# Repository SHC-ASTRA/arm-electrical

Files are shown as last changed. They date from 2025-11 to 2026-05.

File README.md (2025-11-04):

# Arm Electrical



Includes the KiCAD files for the Socket and Digit PCBs; Socket is located at the base of Arm and controls the Arm's main joints, Digit is located at the end of Arm and controls Wrist and End Effector.

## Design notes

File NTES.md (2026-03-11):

REVs two on bottom two on wall. PCB mounted in spost as current; have esp face outawrds; 
Digit,Digit BATT, and digit CAN near current leds
Encoders in same spot?
fan ports on side of leds.

28.2 mm width
56.5 mm hieght
26.0 mm pins outside width 
54.0 mm pins outside hieght
03.2 mm distance between pins outer
01.9 mm distance between pins inner
00.6 mm pin width

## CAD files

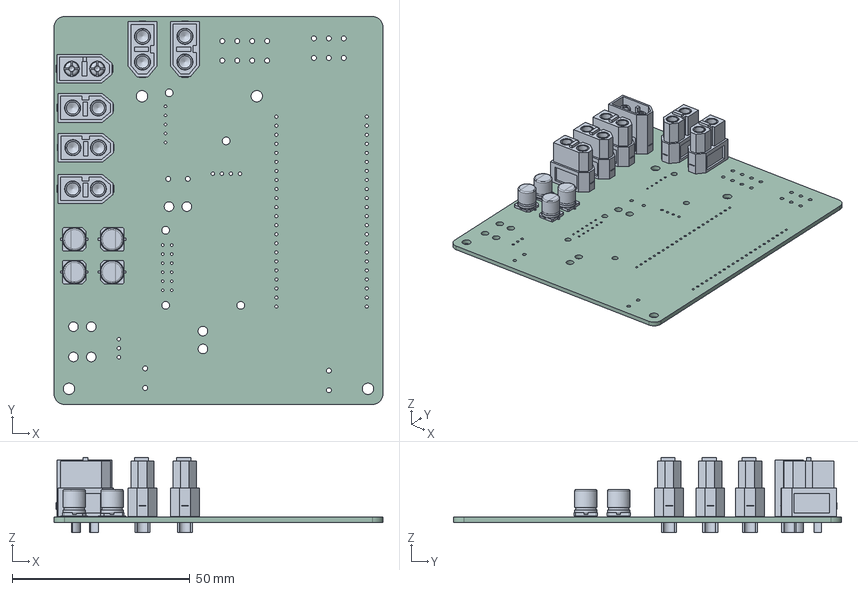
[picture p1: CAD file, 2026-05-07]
Arm/ArmV2.step
92.4 x 109.0 x 21.2 mm
AMASS_XT60-F_1x02_P7.2mm_Vertical x 5
CP_Elec_6.3x7.7 x 4
AMASS_XT60-M_1x02_P7.2mm_Vertical
Arm_PCB

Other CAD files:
Arm/Arm.step

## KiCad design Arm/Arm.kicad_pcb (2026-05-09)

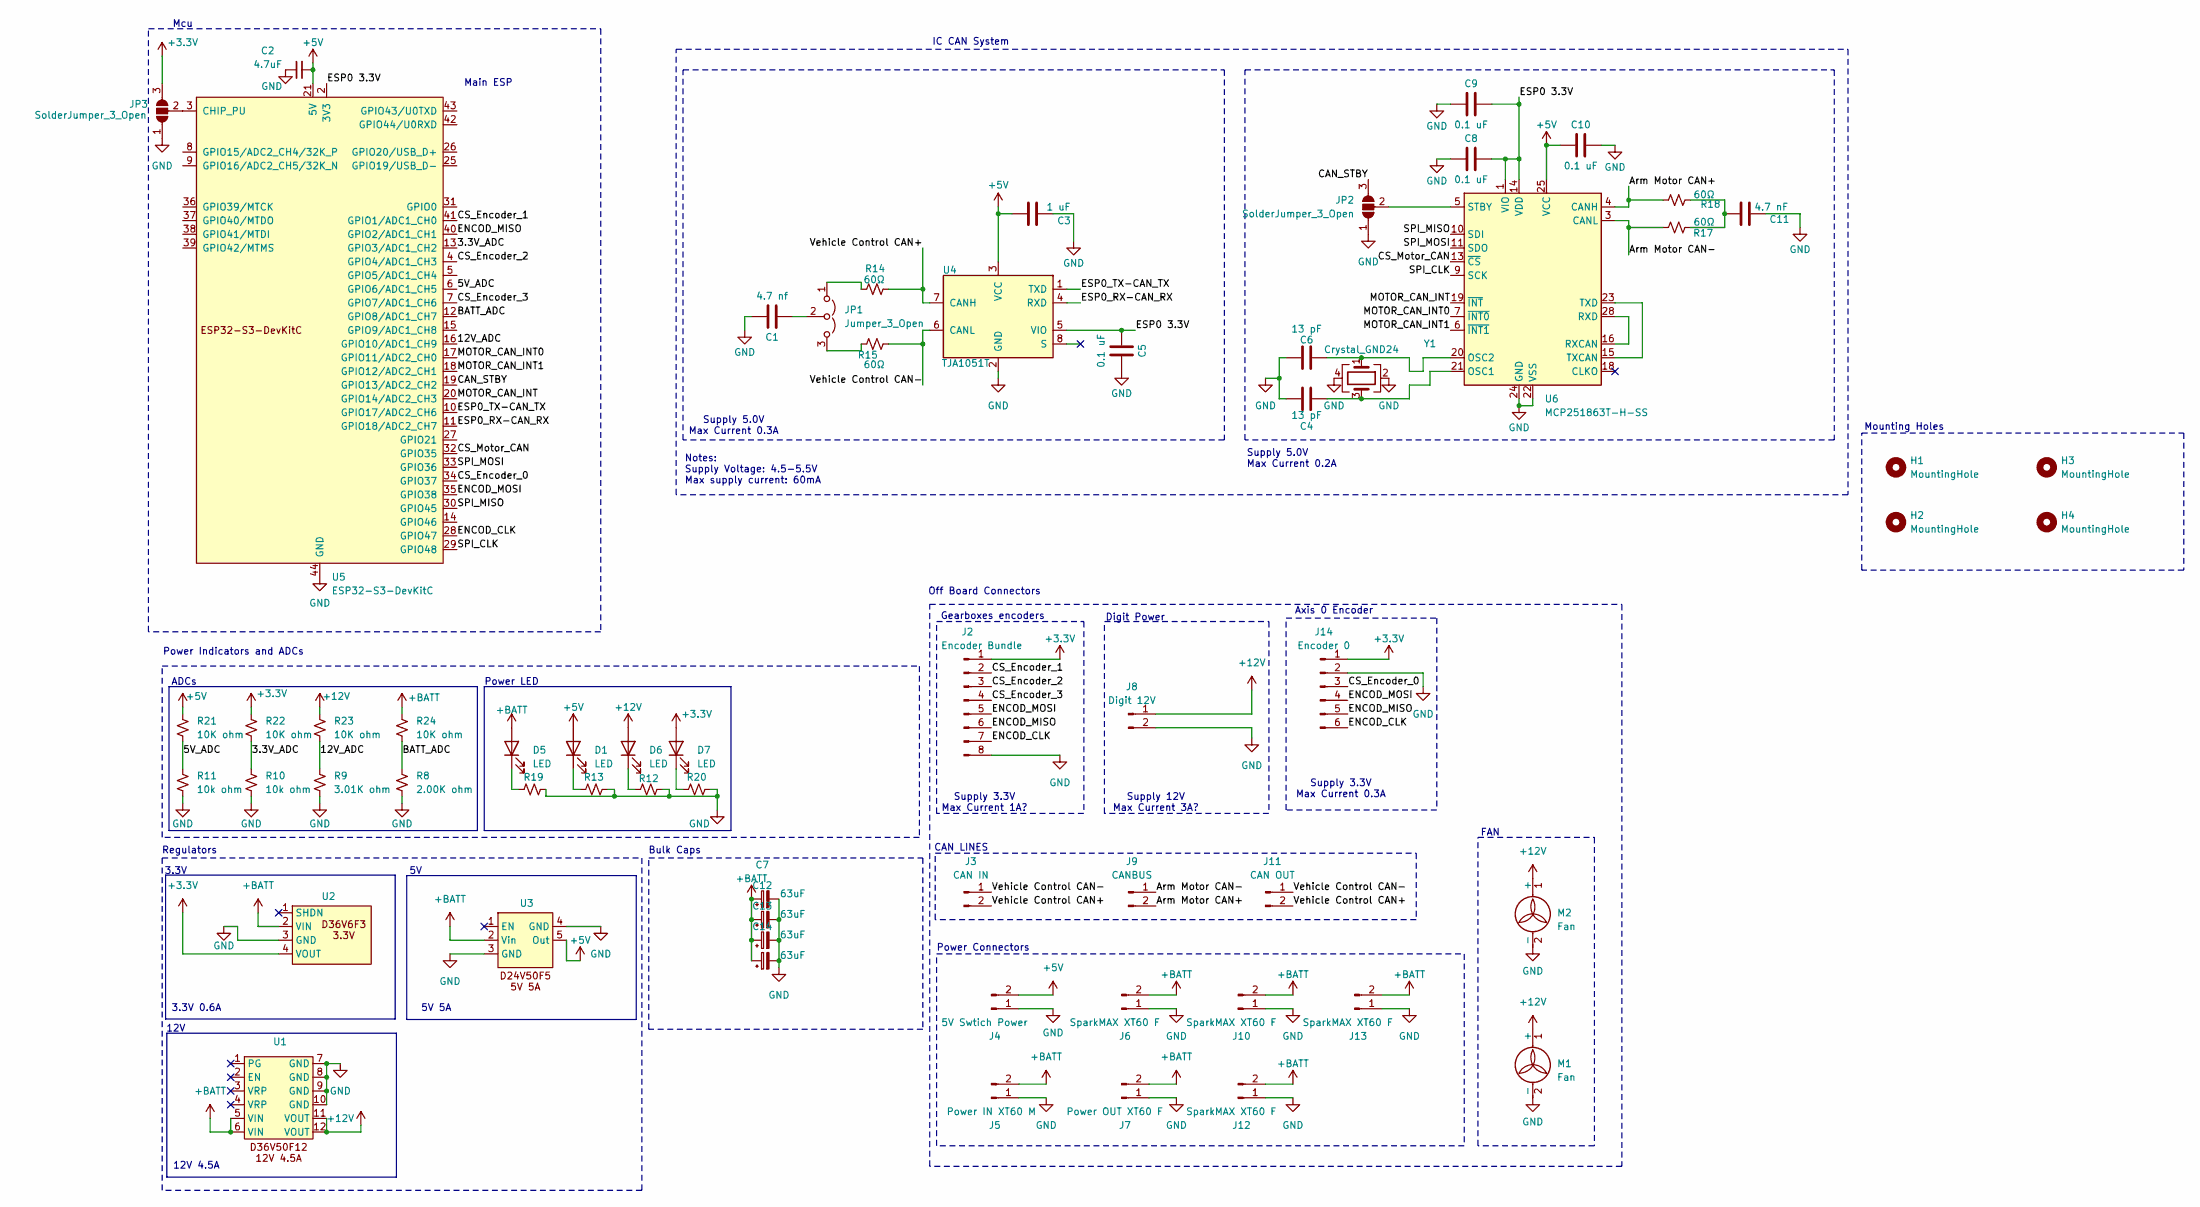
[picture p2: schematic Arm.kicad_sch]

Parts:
C1: 4.7 nf; C_0603_1608Metric_Pad1.08x0.95mm_HandSolder
C2: 4.7uF; C_0603_1608Metric_Pad1.08x0.95mm_HandSolder
C3: 1 uF; C_0603_1608Metric_Pad1.08x0.95mm_HandSolder
C4, C6: 13 pF; C_0603_1608Metric_Pad1.08x0.95mm_HandSolder
C5, C8, C9, C10: 0.1 uF; C_0603_1608Metric_Pad1.08x0.95mm_HandSolder
C7, C12, C13, C14: 63uF; CP_Elec_6.3x7.7
C11: 4.7 nF; C_0603_1608Metric_Pad1.08x0.95mm_HandSolder
D1, D5, D6, D7: LED; LED_0603_1608Metric_Pad1.05x0.95mm_HandSolder
H1, H2, H3, H4: MountingHole; MountingHole_3.2mm_M3_DIN965_Pad_TopBottom
J2: Encoder Bundle; Molex_Mini-Fit_Jr_5566-08A_2x04_P4.20mm_Vertical
J3: CAN IN; AMASS_XT30U-F_1x02_P5.0mm_Vertical
J4: 5V Swtich Power; Molex_Mini-Fit_Jr_5566-02A_2x01_P4.20mm_Vertical
J5: Power IN XT60 M; AMASS_XT60-M_1x02_P7.20mm_Vertical
J6, J10, J12, J13: SparkMAX XT60 F; AMASS_XT60-F_1x02_P7.20mm_Vertical
J7: Power OUT XT60 F; AMASS_XT60-F_1x02_P7.20mm_Vertical
J8: Digit 12V; AMASS_XT30U-F_1x02_P5.0mm_Vertical
J9: CANBUS; AMASS_XT30U-F_1x02_P5.0mm_Vertical
J11: CAN OUT; AMASS_XT30U-F_1x02_P5.0mm_Vertical
J14: Encoder 0; Molex_Mini-Fit_Jr_5566-06A_2x03_P4.20mm_Vertical
JP1: Jumper_3_Open; PinHeader_1x03_P2.54mm_Vertical
JP2, JP3: SolderJumper_3_Open; SolderJumper-3_P1.3mm_Open_RoundedPad1.0x1.5mm
M1, M2: Fan; Molex_Mini-Fit_Jr_5566-02A_2x01_P4.20mm_Vertical
R8: 2.00K ohm; R_0603_1608Metric_Pad0.98x0.95mm_HandSolder
R9: 3.01K ohm; R_0603_1608Metric_Pad0.98x0.95mm_HandSolder
R10, R11: 10k ohm; R_0603_1608Metric_Pad0.98x0.95mm_HandSolder
R12, R13, R20: R_Small_US; R_0603_1608Metric_Pad0.98x0.95mm_HandSolder
R14, R15, R17, R18: 60Ω; R_0603_1608Metric_Pad0.98x0.95mm_HandSolder
R19: 2k ohm; R_0603_1608Metric_Pad0.98x0.95mm_HandSolder
R21, R22, R23, R24: 10K ohm; R_0603_1608Metric_Pad0.98x0.95mm_HandSolder
U1: D36V50F12
U2: D36V6F3 3.3V
U3: D24V50F5
U4: TJA1051T; SOIC-8_3.9x4.9mm_P1.27mm
U5: ESP32-S3-DevKitC
U6: MCP251863T-H-SS; SSOP-28_5.3x10.2mm_P0.65mm
Y1: Crystal_GND24; Crystal_SMD_3225-4Pin_3.2x2.5mm_HandSoldering

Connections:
+3.3V: D7.2 (A), J2.1, J14.1, JP3.3 (B), R22.1, U2.4 (VOUT)
+5V: C2.2, C3.1, C10.2, D1.2 (A), J4.2, R21.1, U3.5 (Out), U4.3 (VCC), U5.21 (5V), U6.25 (VCC)
+12V: D6.2 (A), J8.1, M1.1 (+), M2.1 (+), R23.1, U1.11 (VOUT), U1.12 (VOUT)
+BATT: C7.1, C12.1, C13.1, C14.1, D5.2 (A), J5.2, J6.2, J7.2, J10.2, J12.2, J13.2, R24.1, U1.5 (VIN), U1.6 (VIN), U2.2 (VIN), U3.2 (Vin)
/3.3V_ADC: R10.1, R22.2, U5.13 (GPIO3/ADC1_CH2)
/5V_ADC: R11.1, R21.2, U5.6 (GPIO6/ADC1_CH5)
/12V_ADC: R9.1, R23.2, U5.16 (GPIO10/ADC1_CH9)
/Arm Motor CAN+: J9.2, R18.2, U6.4 (CANH)
/Arm Motor CAN-: J9.1, R17.1, U6.3 (CANL)
/BATT_ADC: R8.1, R24.2, U5.12 (GPIO8/ADC1_CH7)
/CAN_STBY: JP2.3 (B), U5.19 (GPIO13/ADC2_CH2)
/CS_Encoder_0: J14.3, U5.34 (GPIO37)
/CS_Encoder_1: J2.2, U5.41 (GPIO1/ADC1_CH0)
/CS_Encoder_2: J2.3, U5.4 (GPIO4/ADC1_CH3)
/CS_Encoder_3: J2.4, U5.7 (GPIO7/ADC1_CH6)
/CS_Motor_CAN: U5.32 (GPIO35), U6.13 (~CS)
/ENCOD_CLK: J2.7, J14.6, U5.28 (GPIO47)
/ENCOD_MISO: J2.6, J14.5, U5.40 (GPIO2/ADC1_CH1)
/ENCOD_MOSI: J2.5, J14.4, U5.35 (GPIO38)
/ESP0 3.3V: C5.2, C8.1, C9.1, U4.5 (VIO), U5.1 (3V3), U5.2 (3V3), U6.1 (VIO), U6.14 (VDD)
/ESP0_RX-CAN_RX: U4.4 (RXD), U5.11 (GPIO18/ADC2_CH7)
/ESP0_TX-CAN_TX: U4.1 (TXD), U5.10 (GPIO17/ADC2_CH6)
/MOTOR_CAN_INT: U5.20 (GPIO14/ADC2_CH3), U6.19 (~INT)
/MOTOR_CAN_INT0: U5.17 (GPIO11/ADC2_CH0), U6.7 (~INT0)
/MOTOR_CAN_INT1: U5.18 (GPIO12/ADC2_CH1), U6.6 (~INT1)
/SPI_CLK: U5.29 (GPIO48), U6.9 (SCK)
/SPI_MISO: U5.30 (GPIO45), U6.10 (SDI)
/SPI_MOSI: U5.33 (GPIO36), U6.11 (SDO)
/Vehicle Control CAN+: J3.2, J11.2, R14.1, U4.7 (CANH)
/Vehicle Control CAN-: J3.1, J11.1, R15.2, U4.6 (CANL)
GND: C1.1, C2.1, C3.2, C4.1, C5.1, C6.1, C7.2, C8.2, C9.2, C10.1, C11.1, C12.2, C13.2, C14.2, J2.8, J4.1, J5.1, J6.1, J7.1, J8.2, J10.1, J12.1, J13.1, J14.2, JP2.1 (A), JP3.1 (A), M1.2 (-), M2.2 (-), R8.2, R9.2, R10.2, R11.2, R12.2, R13.2, R19.2, R20.2, U1.7 (GND), U1.8 (GND), U1.9 (GND), U1.10 (GND), U2.3 (GND), U3.3 (GND), U3.4 (GND), U4.2 (GND), U5.22 (GND), U5.23 (GND), U5.24 (GND), U5.44 (GND), U6.22 (VSS), U6.24 (GND), Y1.2, Y1.4
unnamed: C11.2, R17.2, R18.1
unnamed: D1.1 (K), R13.1
unnamed: D5.1 (K), R19.1
unnamed: D6.1 (K), R12.1
unnamed: D7.1 (K), R20.1
unnamed: JP1.1 (A), R14.2
unnamed: JP1.3 (B), R15.1
unnamed: C1.2, JP1.2 (C)
unnamed: JP2.2 (C), U6.5 (STBY)
unnamed: JP3.2 (C), U5.3 (CHIP_PU)
unnamed: C4.2, U6.21 (OSC1), Y1.3
unnamed: C6.2, U6.20 (OSC2), Y1.1
unnamed: U6.16 (RXCAN), U6.28 (RXD)
unnamed: U6.15 (TXCAN), U6.23 (TXD)

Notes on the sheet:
Supply 5.0V Max Current 0.2A
IC CAN System
CAN LINES
Power LED
Digit Power
3.3V 0.6A
12V
ADCs
Mcu
Notes: Supply Voltage: 4.5-5.5V Max supply current: 60mA
Bulk Caps
Supply 3.3V Max Current 0.3A
Off Board Connectors
Main ESP
Regulators
Axis 0 Encoder
5V 5A
Power Indicators and ADCs
12V 4.5A
Gearboxes encoders
Power Connectors
Mounting Holes
Supply 3.3V Max Current 1A?
Supply 5.0V Max Current 0.3A
Supply 12V Max Current 3A?
FAN
3.3V

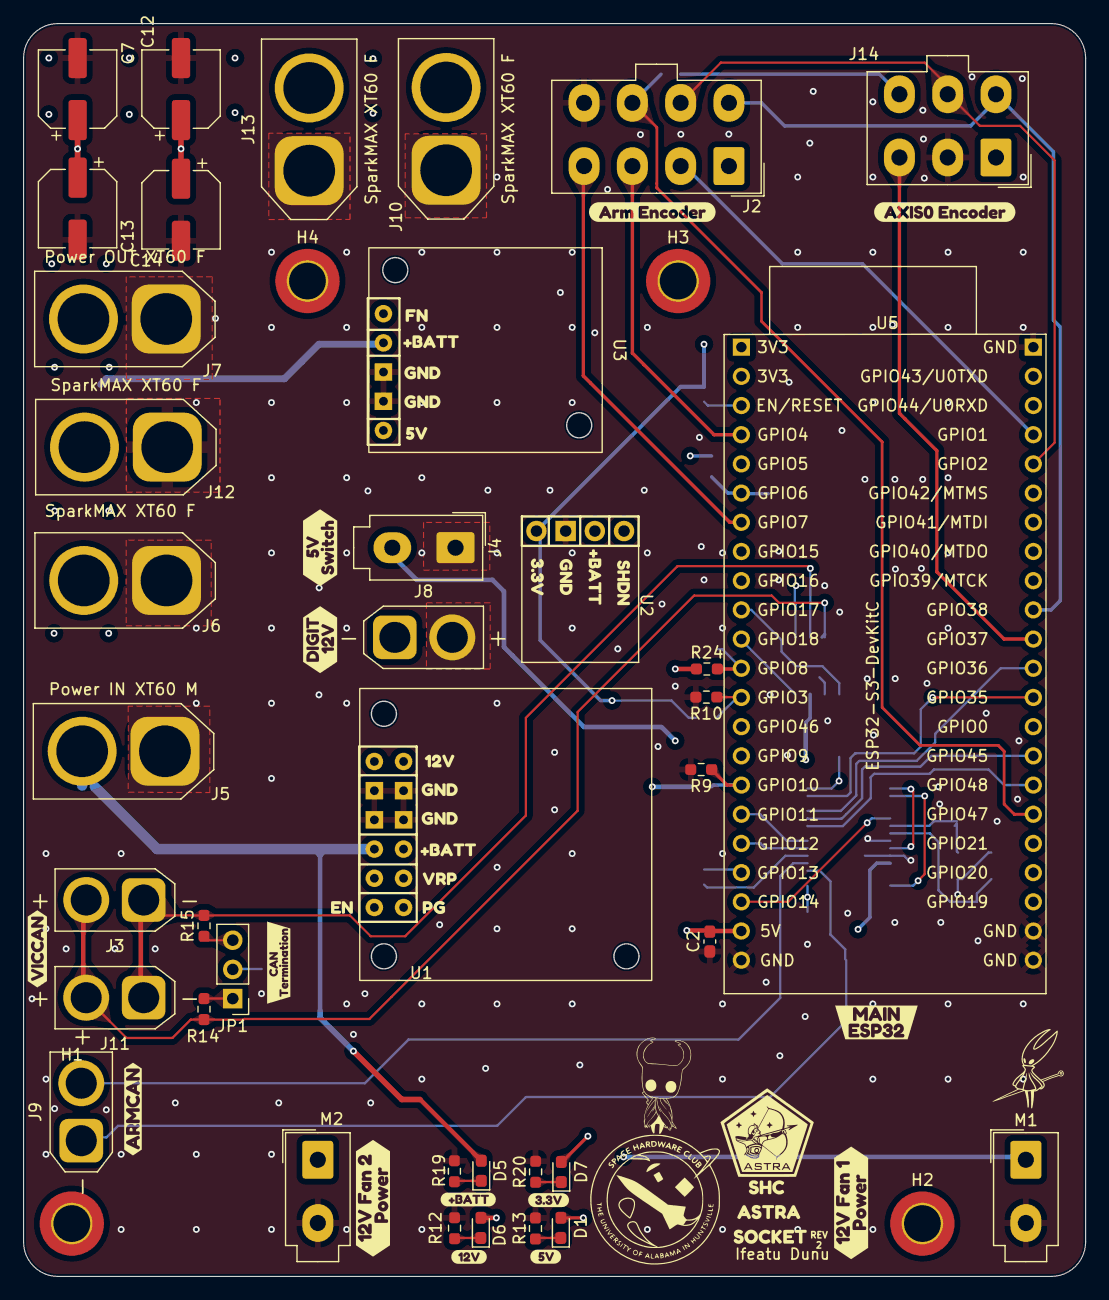
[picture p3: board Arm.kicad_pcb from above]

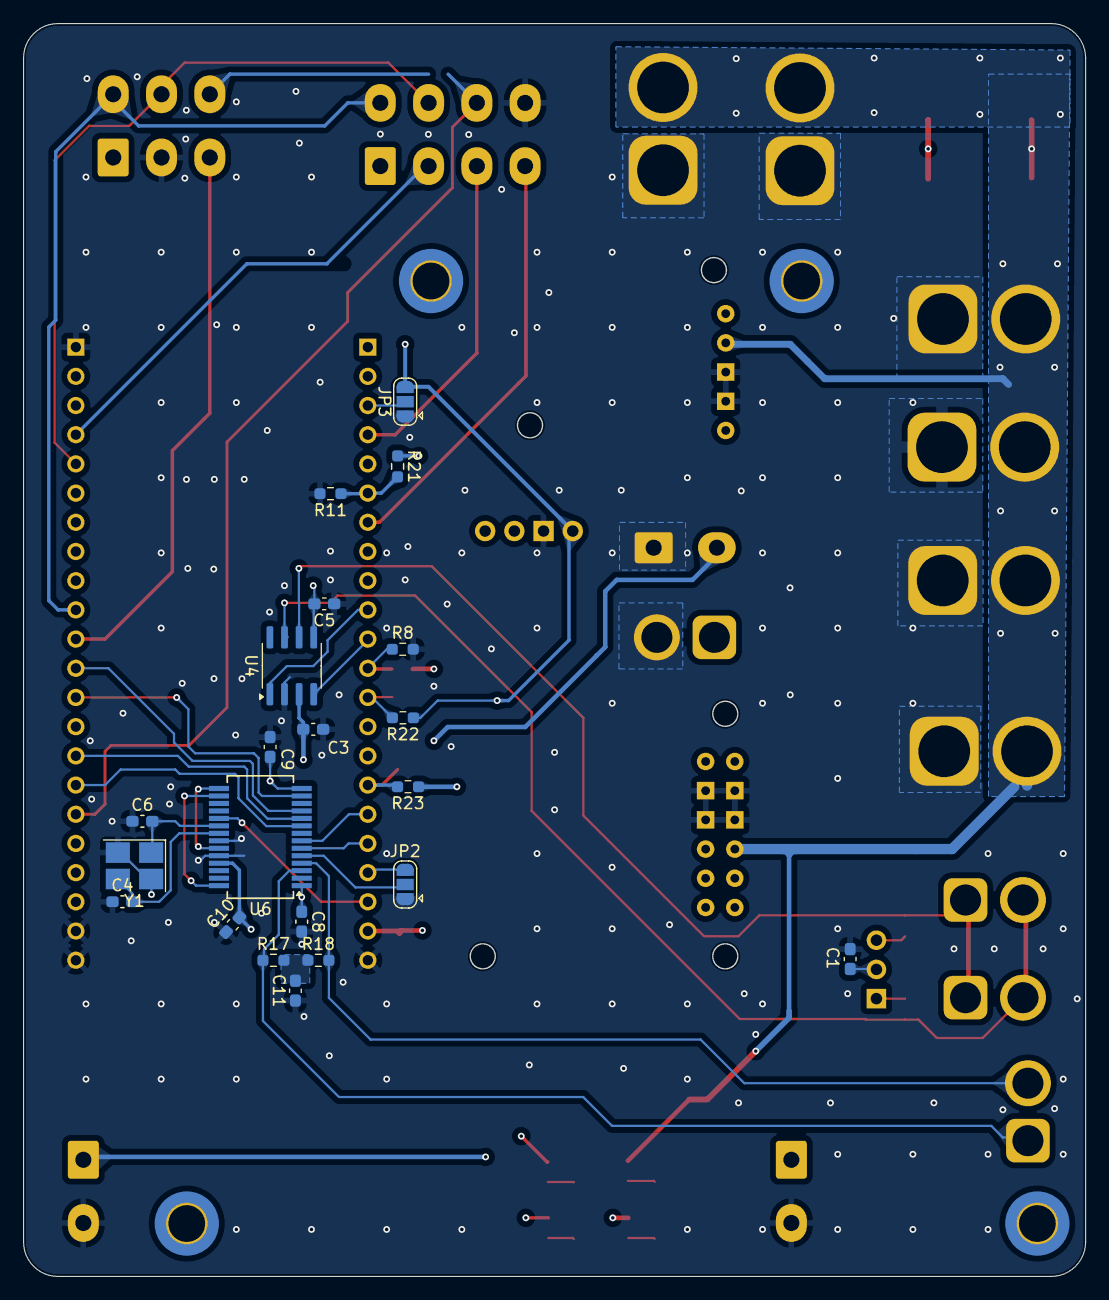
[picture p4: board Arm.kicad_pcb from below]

Board: 4 copper layers, 92.4 x 109.0 mm, 94 parts (21 on the bottom side), 45 nets.

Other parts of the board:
kibuzzard-69B0C619: G***; kibuzzard-69B0C619
kibuzzard-69CF1CE3: G***; kibuzzard-69CF1CE3
kibuzzard-69CF1F55: G***; kibuzzard-69CF1F55
kibuzzard-696ED4E2: G***; kibuzzard-696ED4E2
kibuzzard-696ED4F2: G***; kibuzzard-696ED4F2
kibuzzard-696ED4F9: G***; kibuzzard-696ED4F9
kibuzzard-696ED8B0: G***; kibuzzard-696ED8B0
kibuzzard-696EDF62: G***; kibuzzard-696EDF62
kibuzzard-696EDF69: G***; kibuzzard-696EDF69
kibuzzard-696EDF70: G***; kibuzzard-696EDF70
kibuzzard-696EDFA6: G***; kibuzzard-696EDFA6
kibuzzard-696EDFDB: G***; kibuzzard-696EDFDB
kibuzzard-696EDFE7: G***; kibuzzard-696EDFE7
kibuzzard-696EDFF0: G***; kibuzzard-696EDFF0
kibuzzard-696EE00B: G***; kibuzzard-696EE00B
kibuzzard-696EEF9E: G***; kibuzzard-696EEF9E
kibuzzard-696EEFE3: G***; kibuzzard-696EEFE3
kibuzzard-696EF04A: G***; kibuzzard-696EF04A
kibuzzard-696EF05A: G***; kibuzzard-696EF05A
kibuzzard-699F8EAF: G***; kibuzzard-699F8EAF
kibuzzard-69541FE4: G***; kibuzzard-69541FE4
kibuzzard-69701E52: G***; kibuzzard-69701E52
kibuzzard-69783B26: G***; kibuzzard-69783B26
kibuzzard-697025BA: G***; kibuzzard-697025BA
kibuzzard-6954203E: G***; kibuzzard-6954203E
kibuzzard-6970222E: G***; kibuzzard-6970222E
kibuzzard-6970240E: G***; kibuzzard-6970240E
kibuzzard-69542020, kibuzzard-69542020#2: G***; kibuzzard-69542020
kibuzzard-69702208: G***; kibuzzard-69702208
kibuzzard-69702591: G***; kibuzzard-69702591

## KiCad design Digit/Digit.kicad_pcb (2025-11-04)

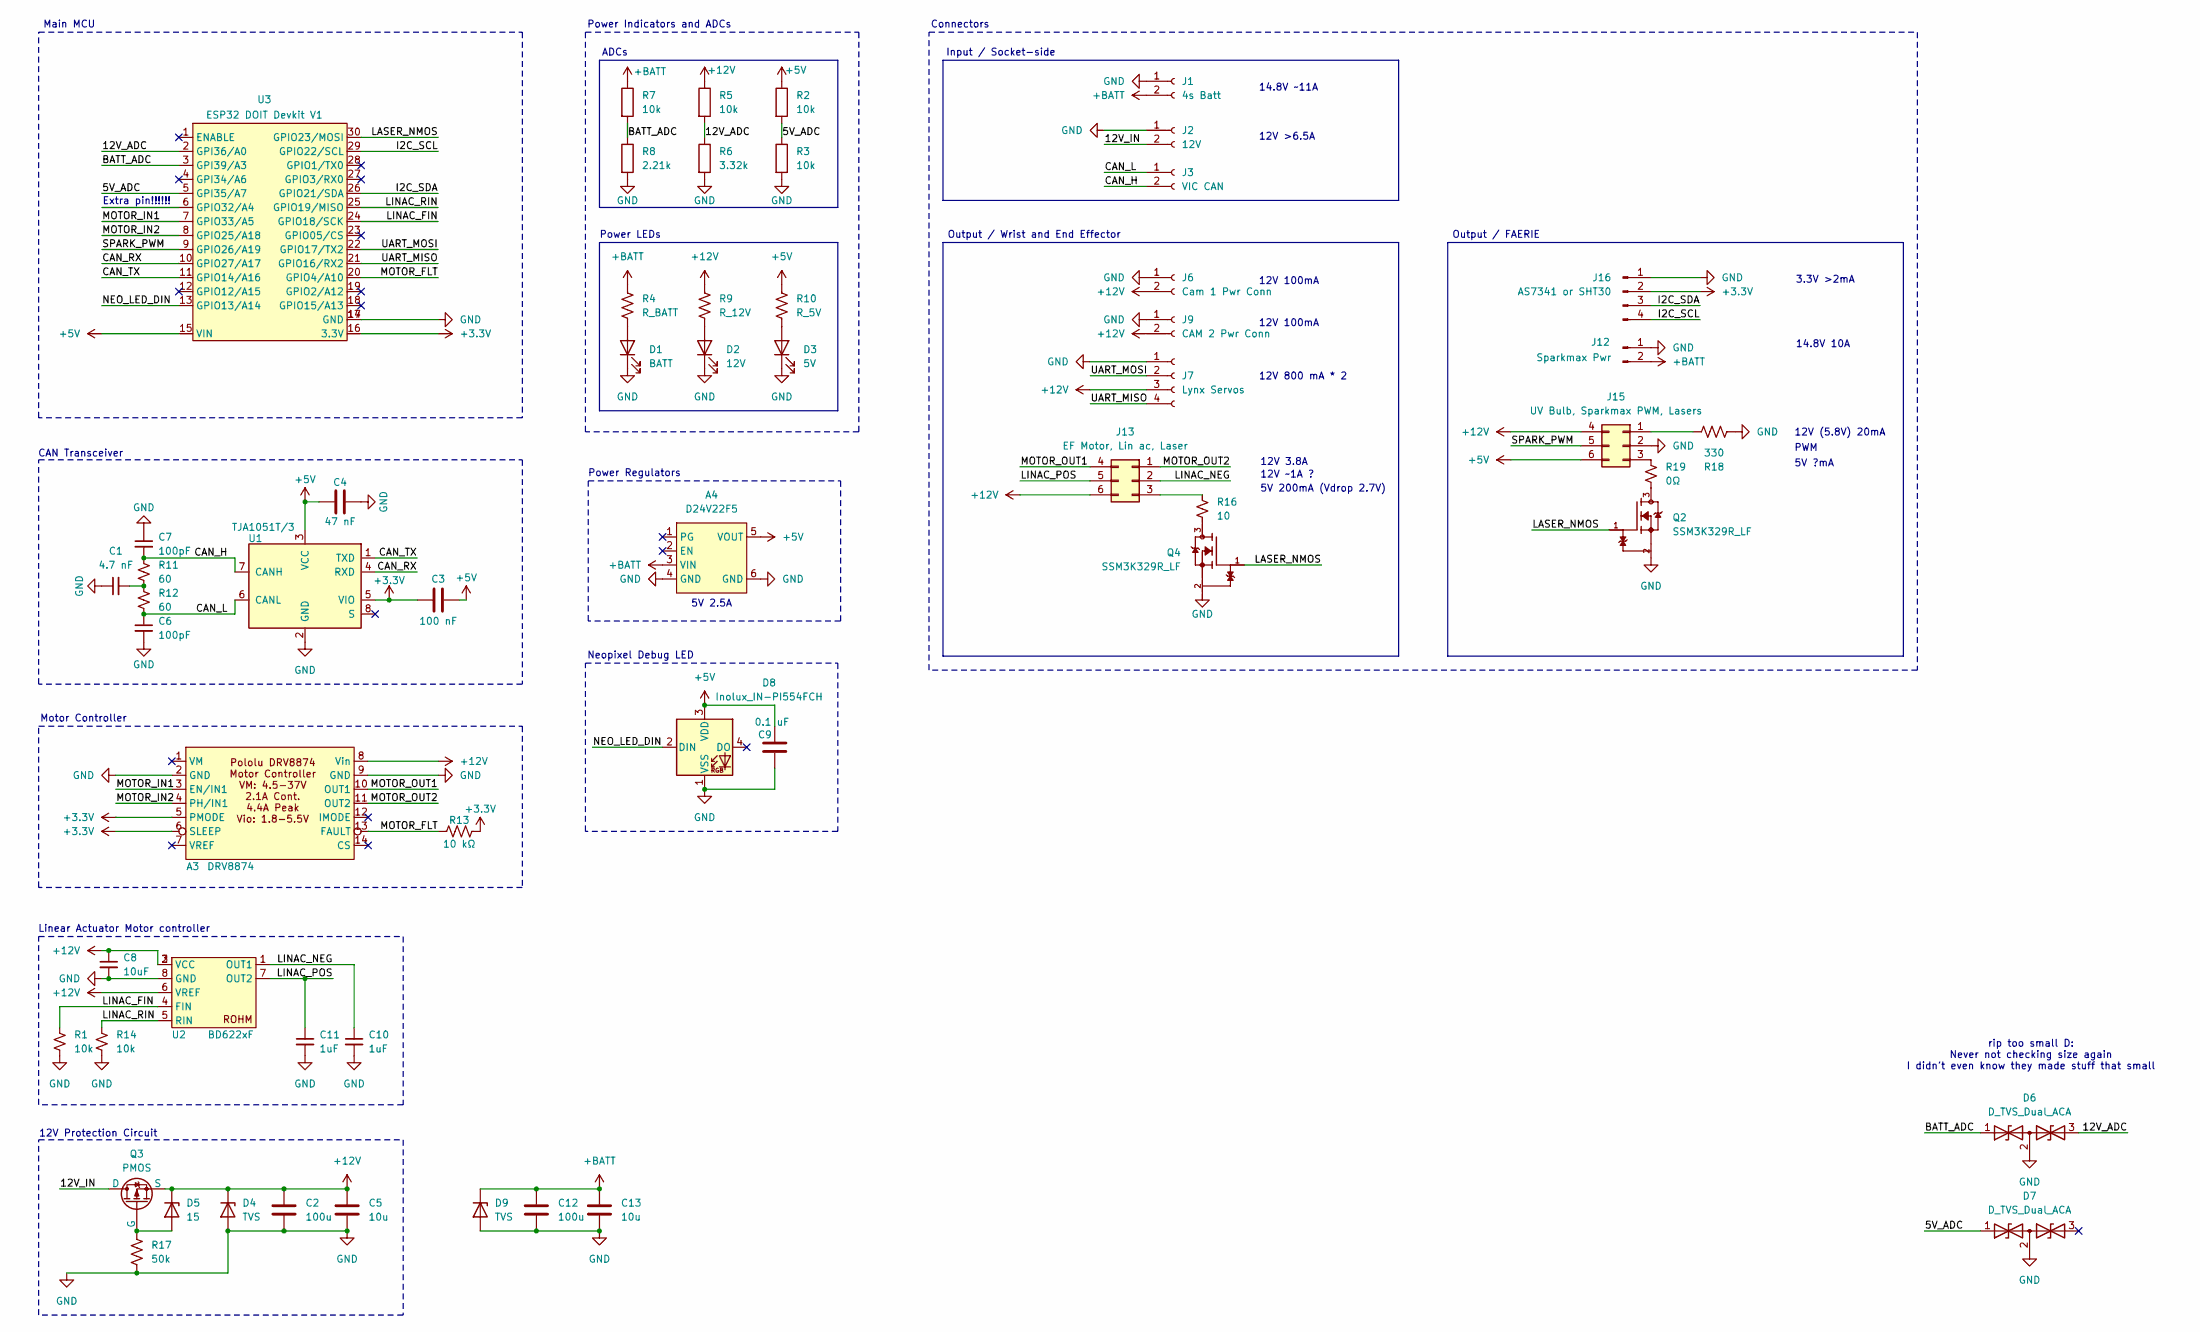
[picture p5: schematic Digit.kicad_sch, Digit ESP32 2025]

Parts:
A3: DRV8874
A4: D24V22F5; D24V22Fx
C1: 4.7 nF; C_0603_1608Metric_Pad1.08x0.95mm_HandSolder
C2, C12: 100u; C_0603_1608Metric_Pad1.08x0.95mm_HandSolder
C3: 100 nF; C_0603_1608Metric_Pad1.08x0.95mm_HandSolder
C4: 47 nF; C_0603_1608Metric_Pad1.08x0.95mm_HandSolder
C5, C13: 10u; C_0603_1608Metric_Pad1.08x0.95mm_HandSolder
C6, C7: 100pF; C_0603_1608Metric_Pad1.08x0.95mm_HandSolder
C8: 10uF; C_0603_1608Metric_Pad1.08x0.95mm_HandSolder
C9: 0.1 uF; C_0603_1608Metric_Pad1.08x0.95mm_HandSolder
C10, C11: 1uF; C_0603_1608Metric_Pad1.08x0.95mm_HandSolder
D1: BATT; LED_0603_1608Metric_Pad1.05x0.95mm_HandSolder
D2: 12V; LED_0603_1608Metric_Pad1.05x0.95mm_HandSolder
D3: 5V; LED_0603_1608Metric_Pad1.05x0.95mm_HandSolder
D4, D9: TVS; SOD-323HEUS2H_TOS
D5: 15; D_SOD-123
D6, D7: D_TVS_Dual_ACA; SG-WLL-3-1
D8: Inolux_IN-PI554FCH; LED_Inolux_IN-PI554FCH_PLCC4_5.0x5.0mm_P3.2mm
J1: 4s Batt; AMASS_XT60PW-M_1x02_P7.20mm_Horizontal
J2: 12V; AMASS_XT30PW-M_1x02_P2.50mm_Horizontal
J3: VIC CAN; AMASS_XT30PW-F_1x02_P2.50mm_Horizontal
J6: Cam 1 Pwr Conn; AMASS_XT30U-F_1x02_P5.0mm_Vertical
J7: Lynx Servos; Molex_Mini-Fit_Jr_5566-04A_2x02_P4.20mm_Vertical
J9: CAM 2 Pwr Conn; AMASS_XT30U-F_1x02_P5.0mm_Vertical
J12: Sparkmax Pwr; AMASS_XT60PW-F_1x02_P7.20mm_Horizontal
J13: EF Motor, Lin ac, Laser; Molex_Mini-Fit_Jr_5566-06A_2x03_P4.20mm_Vertical
J15: UV Bulb, Sparkmax PWM, Lasers; Molex_Mini-Fit_Jr_5566-06A_2x03_P4.20mm_Vertical
J16: AS7341 or SHT30; Molex_Mini-Fit_Jr_5566-04A_2x02_P4.20mm_Vertical
Q2, Q4: SSM3K329R_LF; SOT-23F_TOS; PARTREV 1.0
Q3: PMOS; TO-252-2
R1, R2, R3, R5, R7, R14: 10k; R_0603_1608Metric_Pad0.98x0.95mm_HandSolder
R4: R_BATT; R_0603_1608Metric_Pad0.98x0.95mm_HandSolder
R6: 3.32k; R_0603_1608Metric_Pad0.98x0.95mm_HandSolder
R8: 2.21k; R_0603_1608Metric_Pad0.98x0.95mm_HandSolder
R9: R_12V; R_0603_1608Metric_Pad0.98x0.95mm_HandSolder
R10: R_5V; R_0603_1608Metric_Pad0.98x0.95mm_HandSolder
R11, R12: 60; R_0603_1608Metric_Pad0.98x0.95mm_HandSolder
R13: 10 kΩ; R_0603_1608Metric_Pad0.98x0.95mm_HandSolder
R16: 10; R_0603_1608Metric_Pad0.98x0.95mm_HandSolder
R17: 50k; R_0603_1608Metric_Pad0.98x0.95mm_HandSolder
R18: 330; R_0603_1608Metric_Pad0.98x0.95mm_HandSolder
R19: 0Ω; R_0603_1608Metric_Pad0.98x0.95mm_HandSolder
U1: TJA1051T/3; SOIC-8_3.9x4.9mm_P1.27mm
U2: BD622xF; SOP8_ROM
U3: ESP32 DOIT Devkit V1; esp32_devkit_v1_doit

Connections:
+3.3V: A3.5 (PMODE), A3.6 (SLEEP), C3.2, J16.2, R13.1, U1.5 (VIO), U3.16 (3.3V)
+5V: A4.5 (VOUT), C3.1, C4.1, C9.1, D8.3 (VDD), J15.6, R2.1, R10.1, U1.3 (VCC), U3.15 (VIN)
+12V: A3.8 (Vin), C2.1, C5.1, C8.1, D4.1 (K), D5.1 (K), J6.2, J7.3, J9.2, J13.6, J15.4, Q3.3 (S), R5.1, R9.1, U2.2 (VCC), U2.3 (VCC), U2.6 (VREF)
+BATT: A4.3 (VIN), C12.1, C13.1, D9.1 (K), J1.2, J12.2, R4.1, R7.1
/5V_ADC: D7.1 (A1), R2.2, R3.1, U3.5 (GPI35/A7)
/12V_ADC: D6.3 (A2), R5.2, R6.1, U3.2 (GPI36/A0)
/12V_IN: J2.2, Q3.1 (D)
/BATT_ADC: D6.1 (A1), R7.2, R8.1, U3.3 (GPI39/A3)
/CAN_H: C7.2, J3.2, R11.1, U1.7 (CANH)
/CAN_L: C6.1, J3.1, R12.2, U1.6 (CANL)
/CAN_RX: U1.4 (RXD), U3.10 (GPIO27/A17)
/CAN_TX: U1.1 (TXD), U3.11 (GPIO14/A16)
/I2C_SCL: J16.4, U3.29 (GPIO22/SCL)
/I2C_SDA: J16.3, U3.26 (GPIO21/SDA)
/LASER_NMOS: Q2.1, Q4.1, U3.30 (GPIO23/MOSI)
/LINAC_FIN: R1.2, U2.4 (FIN), U3.24 (GPIO18/SCK)
/LINAC_NEG: C10.1, J13.2, U2.1 (OUT1)
/LINAC_POS: C11.1, J13.5, U2.7 (OUT2)
/LINAC_RIN: R14.2, U2.5 (RIN), U3.25 (GPIO19/MISO)
/MOTOR_FLT: A3.13 (FAULT), R13.2, U3.20 (GPIO4/A10)
/MOTOR_IN1: A3.3 (EN/IN1), U3.7 (GPIO33/A5)
/MOTOR_IN2: A3.4 (PH/IN1), U3.8 (GPIO25/A18)
/MOTOR_OUT1: A3.10 (OUT1), J13.4
/MOTOR_OUT2: A3.11 (OUT2), J13.1
/NEO_LED_DIN: D8.2 (DIN), U3.13 (GPIO13/A14)
/SPARK_PWM: J15.5, U3.9 (GPIO26/A19)
/UART_MISO: J7.4, U3.21 (GPIO16/RX2)
/UART_MOSI: J7.2, U3.22 (GPIO17/TX2)
GND: A3.2 (GND), A3.9 (GND), A4.4 (GND), A4.6 (GND), C1.1, C2.2, C4.2, C5.2, C6.2, C7.1, C8.2, C9.2, C10.2, C11.2, C12.2, C13.2, D1.1 (K), D2.1 (K), D3.1 (K), D4.2 (A), D6.2 (common), D7.2 (common), D8.1 (VSS), D9.2 (A), J1.1, J2.1, J6.1, J7.1, J9.1, J12.1, J15.2, J16.1, Q2.2, Q4.2, R1.1, R3.2, R6.2, R8.2, R14.1, R17.2, R18.2, U1.2 (GND), U2.8 (GND), U3.14 (GND), U3.17 (GND)
unnamed: C1.2, R11.2, R12.1
unnamed: D1.2 (A), R4.2
unnamed: D2.2 (A), R9.2
unnamed: D3.2 (A), R10.2
unnamed: D5.2 (A), Q3.2 (G), R17.1
unnamed: J13.3, R16.1
unnamed: J15.1, R18.1
unnamed: J15.3, R19.1
unnamed: Q2.3, R19.2
unnamed: Q4.3, R16.2

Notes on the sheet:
12V (5.8V) 20mA
Input / Socket-side
Power Regulators
PWM
ADCs
12V Protection Circuit
5V 2.5A
3.3V >2mA
14.8V ~11A
Linear Actuator Motor controller
12V 100mA
Motor Controller
CAN Transceiver
12V >6.5A
rip too small D: Never not checking size again I didn't even know they made stuff that small
Power LEDs
5V 200mA (Vdrop 2.7V)
12V ~1A ?
Output / Wrist and End Effector
5V ?mA
Main MCU
12V 3.8A
12V 800 mA * 2
Neopixel Debug LED
14.8V 10A
Power Indicators and ADCs
Extra pin!!!!!!
Output / FAERIE
Connectors

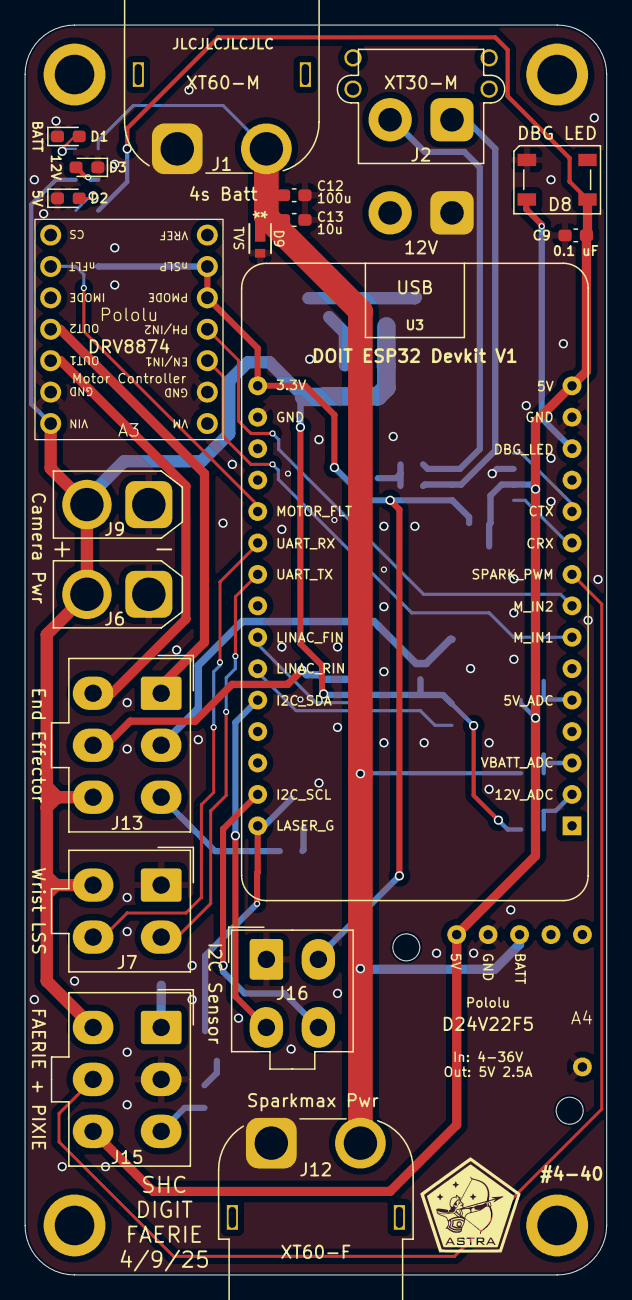
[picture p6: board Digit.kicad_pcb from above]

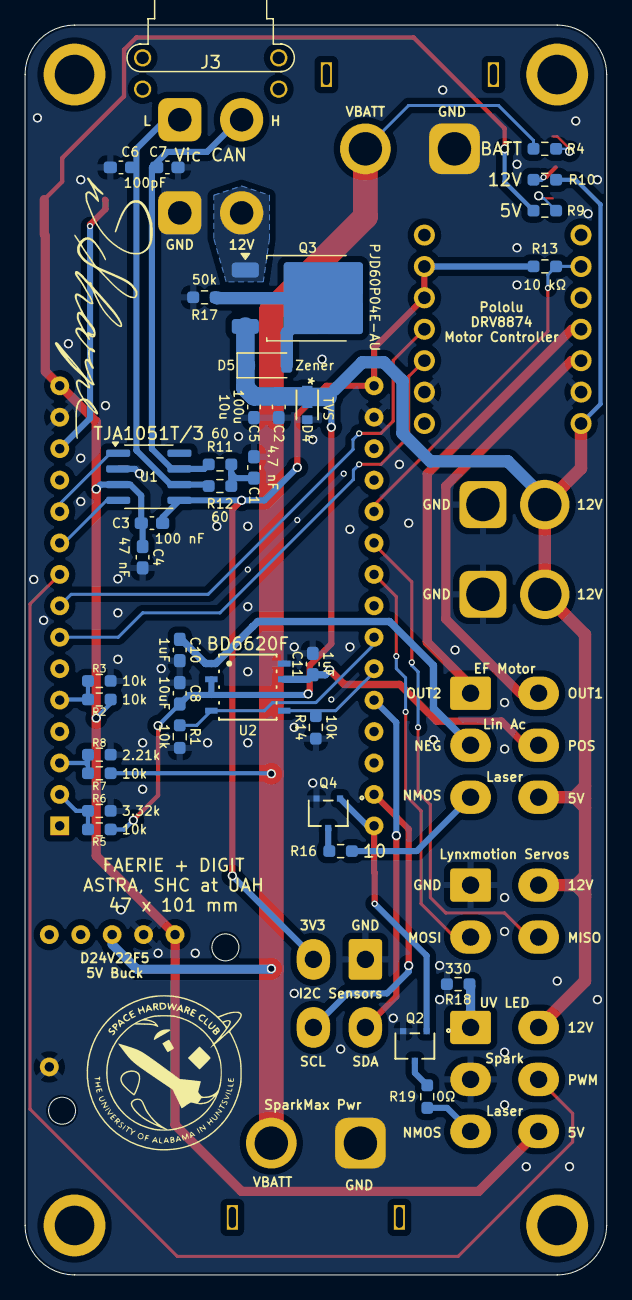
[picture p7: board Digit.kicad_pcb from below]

Board: 2 copper layers, 47.0 x 101.0 mm, 60 parts (36 on the bottom side), 39 nets.

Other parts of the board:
H1, H2, H3, H4: MountingHole_3.2mm_M3

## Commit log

2025-11-04 URC '22
    [039281063.step, 1792245.step, 5v_Supply.sch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]
2025-11-04 URC '24
    [039281063.step, 1792245.step, 5v_Supply.sch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]
2025-11-04 URC '25 - V1
    [Arm.kicad_pcb, Arm.kicad_sch, Astra_Arm_Modulus_Board.kicad_pcb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]
2025-11-04 URC '25 - V2
    [Arm.kicad_pcb, Arm.kicad_sch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]
2025-11-07 PCB Layout....
    [Arm.kicad_pcb, Arm.kicad_sch]
2025-11-14 Progrss on socket -FeedBack Fixes -PCB Layout and signal routing
    [Arm.kicad_pcb, Arm.kicad_sch]
2025-11-16 More Work on PCB
    Moved some stuff around
    [Arm.kicad_pcb, Arm.kicad_sch]
2025-11-18 So Close...
    [Arm.kicad_pcb, Arm.kicad_sch]
2025-11-20 The Unholy PCB
    [Arm.kicad_pcb]
2026-01-05 Had the plague
    [Arm.kicad_pcb, Arm.kicad_sch]
2026-01-07 1 PCB 2 PCB 3 PCB ...
    [Arm.kicad_pcb, Arm.kicad_sch]
2026-01-15 Changes were mostly traces and part spacing
    [Arm.kicad_pcb, Arm.kicad_sch]
2026-01-20 Optimizations
    Some Labesl
    Mounting Holes
    Changed some pins around for short traces
    [Arm-B_Cu.gbl, Arm-B_Mask.gbs, Arm-B_Paste.gbp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]
2026-01-21 Cleaning up things
    [Arm.kicad_pcb]
2026-01-28 Hegale!
    Small optimizations
    [Arm.kicad_pcb]
2026-02-10 Need to swtich to windows
    [Arm.kicad_pcb, Arm.kicad_sch]
2026-02-15 Moving Connectors and small layout changes
    [Arm.kicad_pcb, Arm.kicad_sch]
2026-02-26 1/3 Final Changes
    [Arm.kicad_pcb, Arm.kicad_sch]
2026-03-11 2/3 Final Changes
    [Arm.kicad_pcb, Arm.kicad_sch]
2026-03-17 Final Part 3
    [Arm.kicad_pcb, Arm.kicad_sch]
2026-04-01 Review Changes
    [Arm.kicad_pcb, Arm.kicad_sch]
2026-04-01 Odering Version
    [Arm.kicad_pcb, Arm.kicad_sch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]
2026-04-24 fixes for rev 2
    [Arm.kicad_pcb, Arm.kicad_sch]
2026-05-07 More Changes for REV 2
    [Arm-B_Cu.gbl, Arm-B_Mask.gbs, Arm-B_Paste.gbp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]
2026-05-09 Final REV 2 Pt2
    [Arm.kicad_pcb, Arm.kicad_sch]

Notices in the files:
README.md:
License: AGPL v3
